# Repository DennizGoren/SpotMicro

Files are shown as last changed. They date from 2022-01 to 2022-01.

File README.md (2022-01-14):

# ROS-based SpotMicro 
TU Delft - Mechanical Engineering (Cognitive Robotics) Bachelor's Thesis

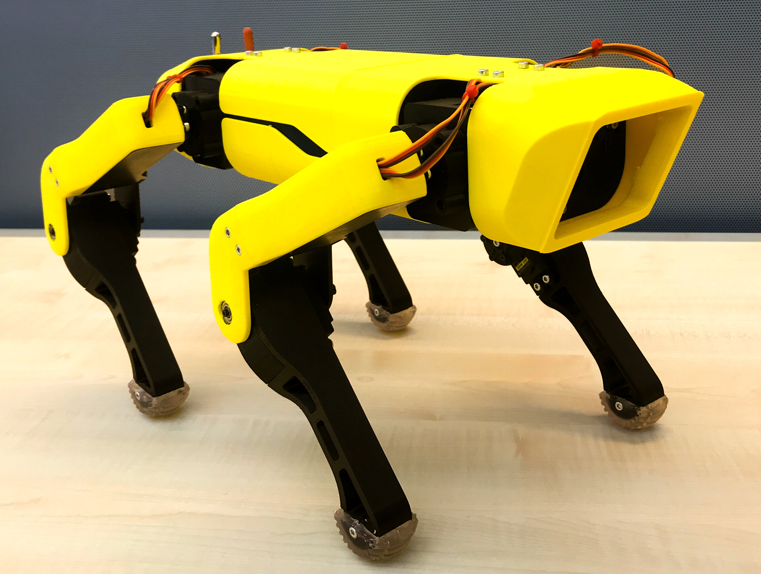
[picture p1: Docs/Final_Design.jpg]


## Introduction
According to 'How robots change the world' by Oxford Economics, Robots could take over 20 million jobs by 2030. It is no longer a question of if robotics will shape our future, but how much and in what ways. This makes teaching young students about robotics all the more important. 

This is the bachelor thesis of four mechanical engineering students of the 3mE faculty at the Delft Technical University. This bachelor thesis was made under the supervision of MSc. Martin Klomp, ir. Ehsan Hosseini and ir. André van der Kraan of the Cognitive Robotics Department.

This report describes the design project called 'Building a low-cost ROS-based Quadruped SpotMicro Robot'. The Cognitive Robotics project has the aim to design a low-cost robot that uses components of the Mirte robot kit. Mirte is a robot developed for education, that includes hardware and software. Mirte was created with the idea that educational robots should be cheap, open source, focus on more than just software, have as few custom parts as possible and should be useful from primary/elementary school all the way to university. 
The Mirte components that are used in the Spotmicro robot are the OrangePi Zero and the STM32 MINI Controller. The software is a python api for ROS, making it possible to control robots from a python script. 

SpotMicro is an opensource robot which takes design elements from the famous spot robot by Boston Dynamics. There are a number of existing designs for the SpotMicro, of which we chose one. Therefore, the design challenge of this project is mostly in research in servo motor selection and the programing of the robot to make SpotMicro work with the Mirte components and software. 

The parts that were used to build the robot were all taken from the SpotMicroESP32 project of Michael Kubina and can be found here:
https://github.com/michaelkubina/SpotMicroESP32

In the simulations folder, the theoretical models for the predictions of the motor torque requirements can be found. All the forward kinametics for the robot control can be found in the code folder. All the STL's that were designed by us for the Mirte hardware can be found in the parts folder.

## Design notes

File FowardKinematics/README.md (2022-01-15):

# Forward Kinematics
The control of the robot was programmed with forward kinematics in Python with the use of the Mirte api for ROS.

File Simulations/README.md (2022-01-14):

In order to predict the minimal required motor torque, multiple
theoretical models were be made. The first model was  a
motion study in Solidworks. Next, a dynamical kinematics
model was be made with the use of Python. From the findings
of the theoretical models, a motor selection was done and
implemented in an actual robot. And lastly, in order to validate
the models, a video analysis of the motion of the robot was
done with the use of Coach 7 and Python.

The SolidWorks motion study modeled the following movements and returned the torques that were deliverd by the motors in the joints. 
The results of this motion study are plotted in the graphs below. 
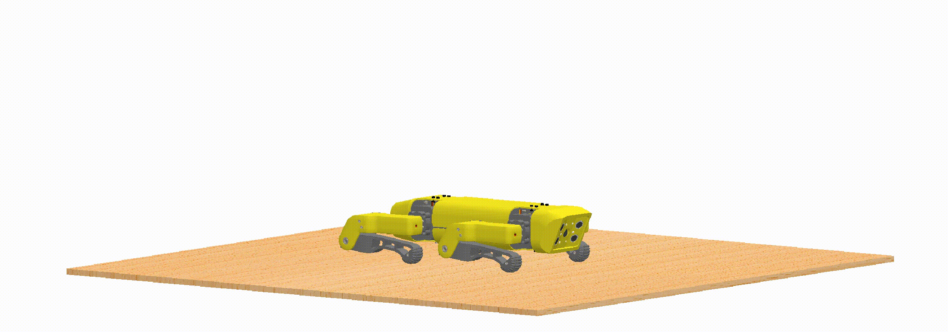
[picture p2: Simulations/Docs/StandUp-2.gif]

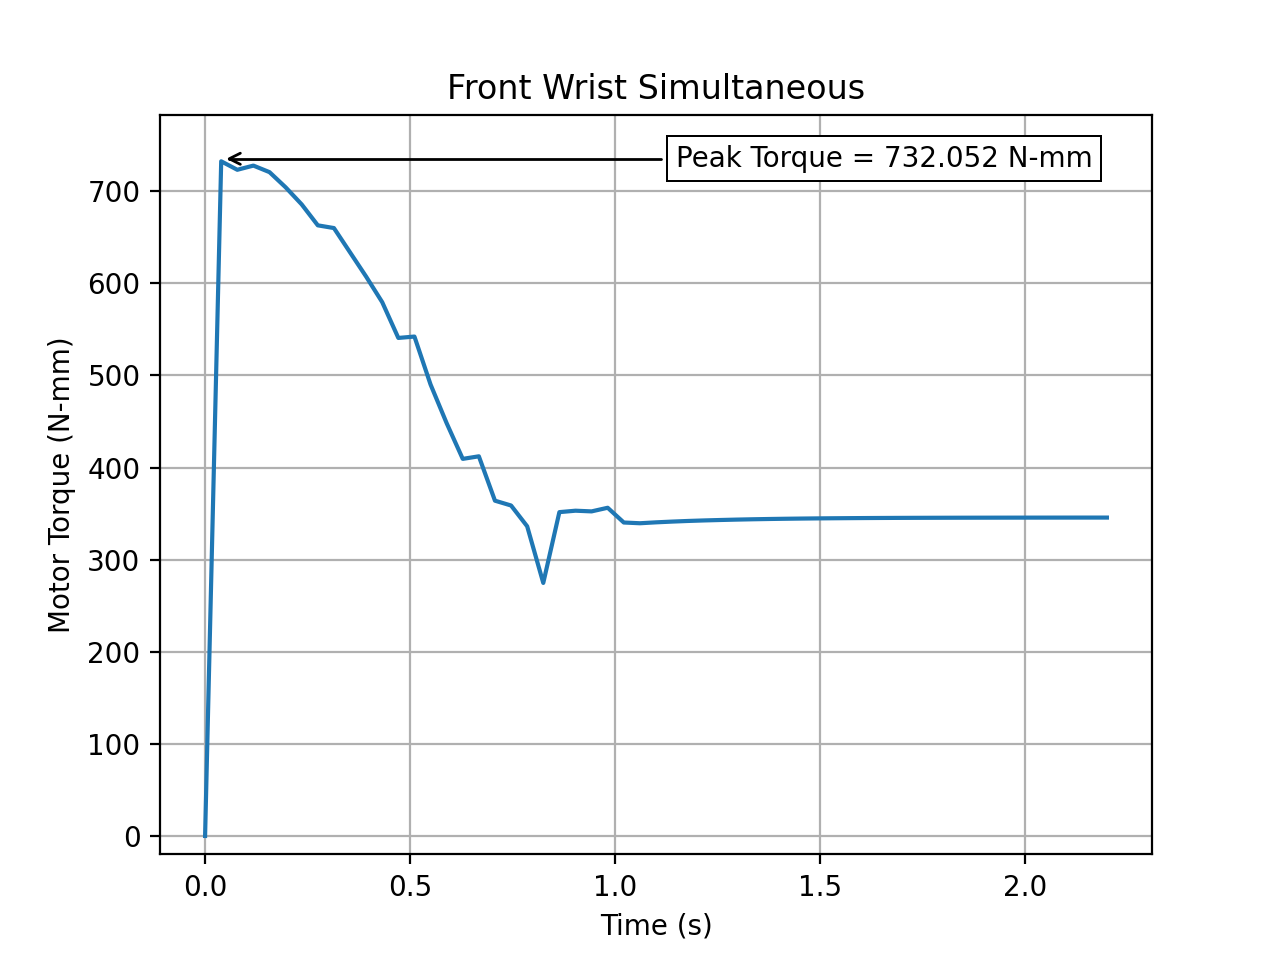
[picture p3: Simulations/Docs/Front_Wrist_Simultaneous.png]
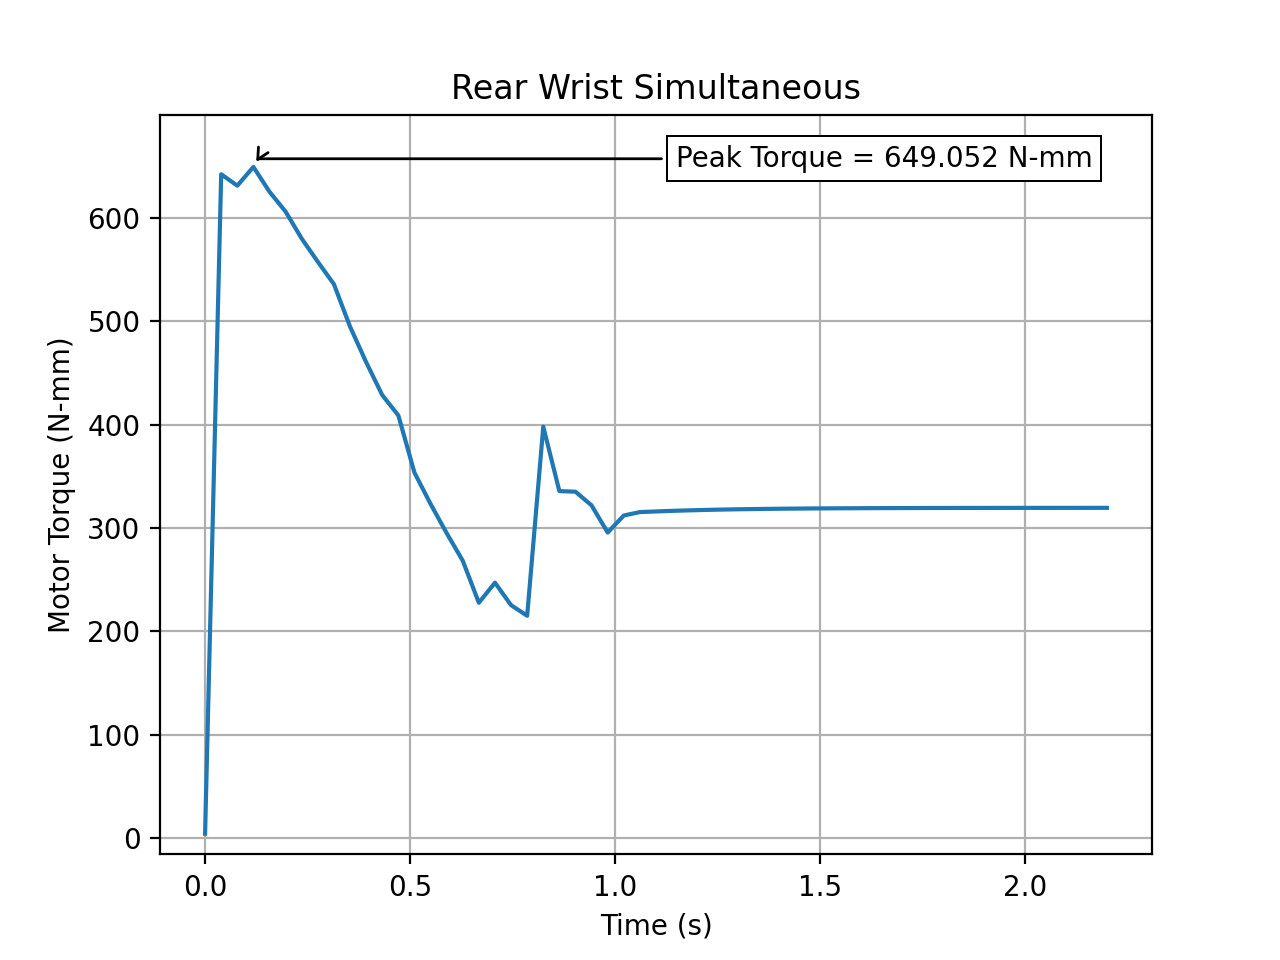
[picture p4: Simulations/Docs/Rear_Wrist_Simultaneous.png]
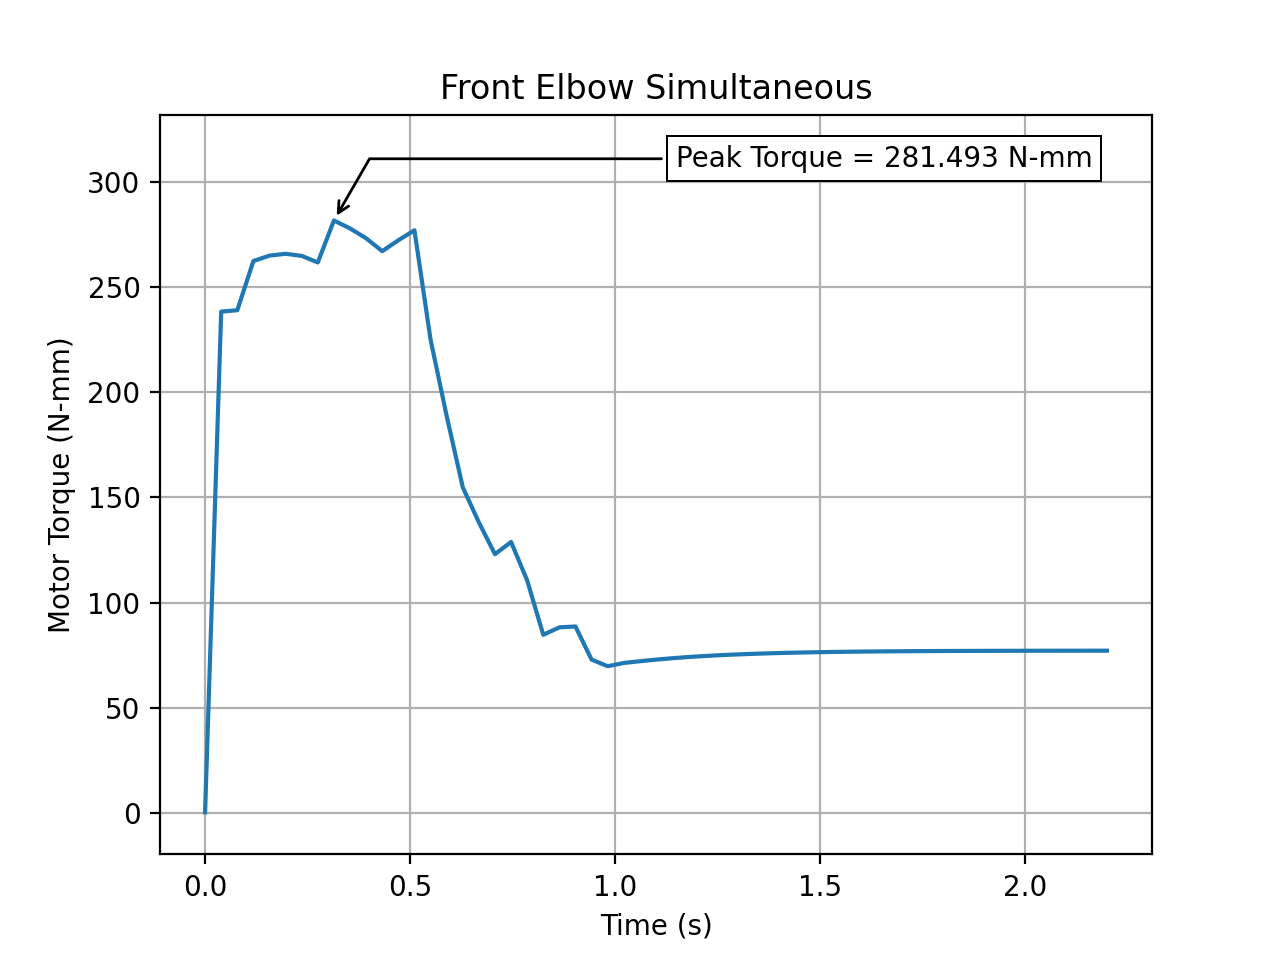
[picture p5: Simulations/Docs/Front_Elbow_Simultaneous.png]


The peak in motor torque is 732 N-mm and witnessed in the wrists of the front legs of the robot.  

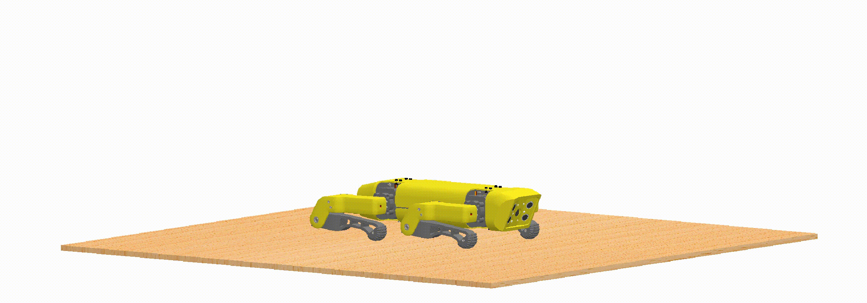
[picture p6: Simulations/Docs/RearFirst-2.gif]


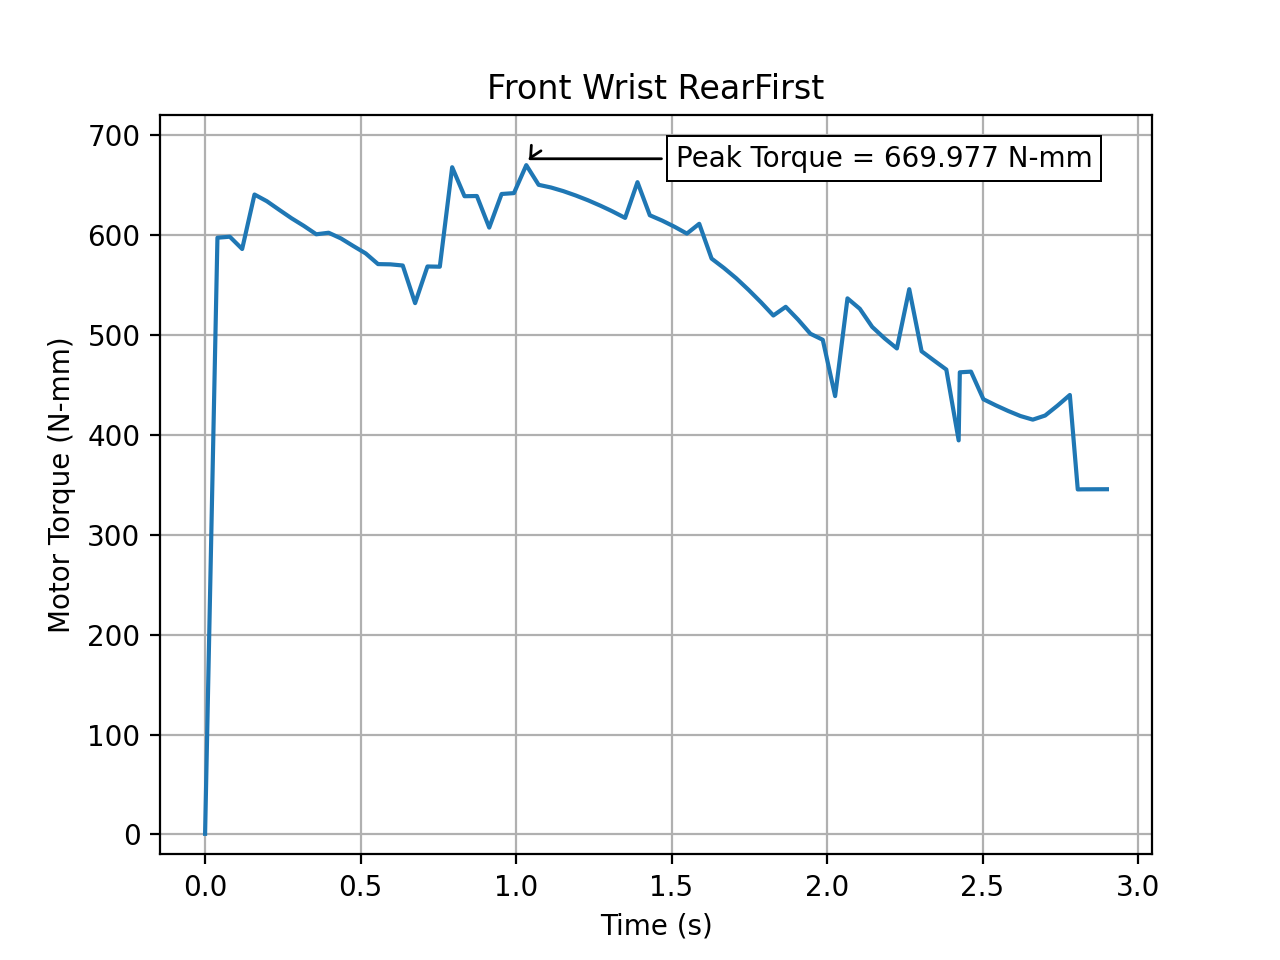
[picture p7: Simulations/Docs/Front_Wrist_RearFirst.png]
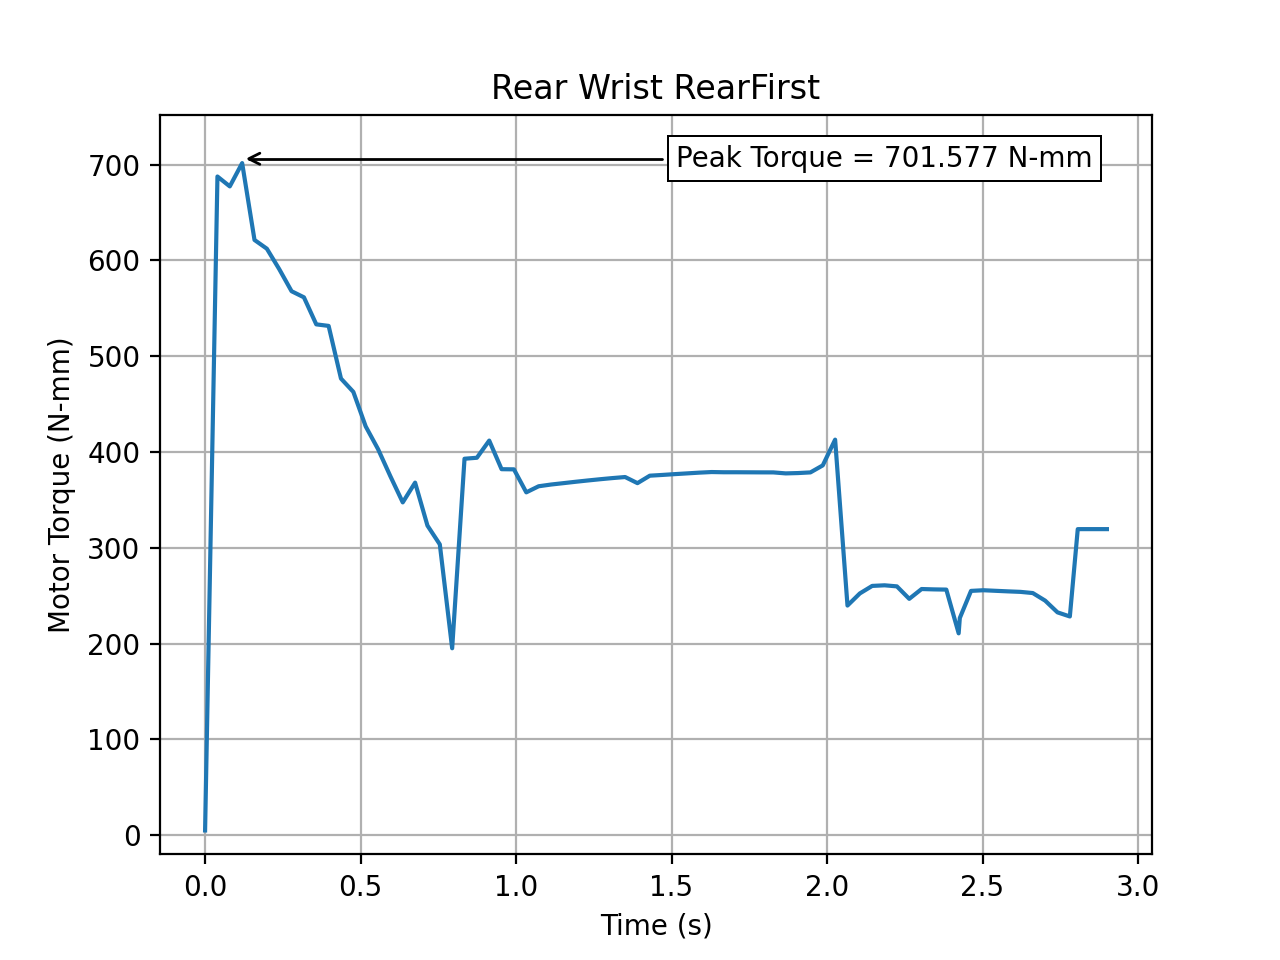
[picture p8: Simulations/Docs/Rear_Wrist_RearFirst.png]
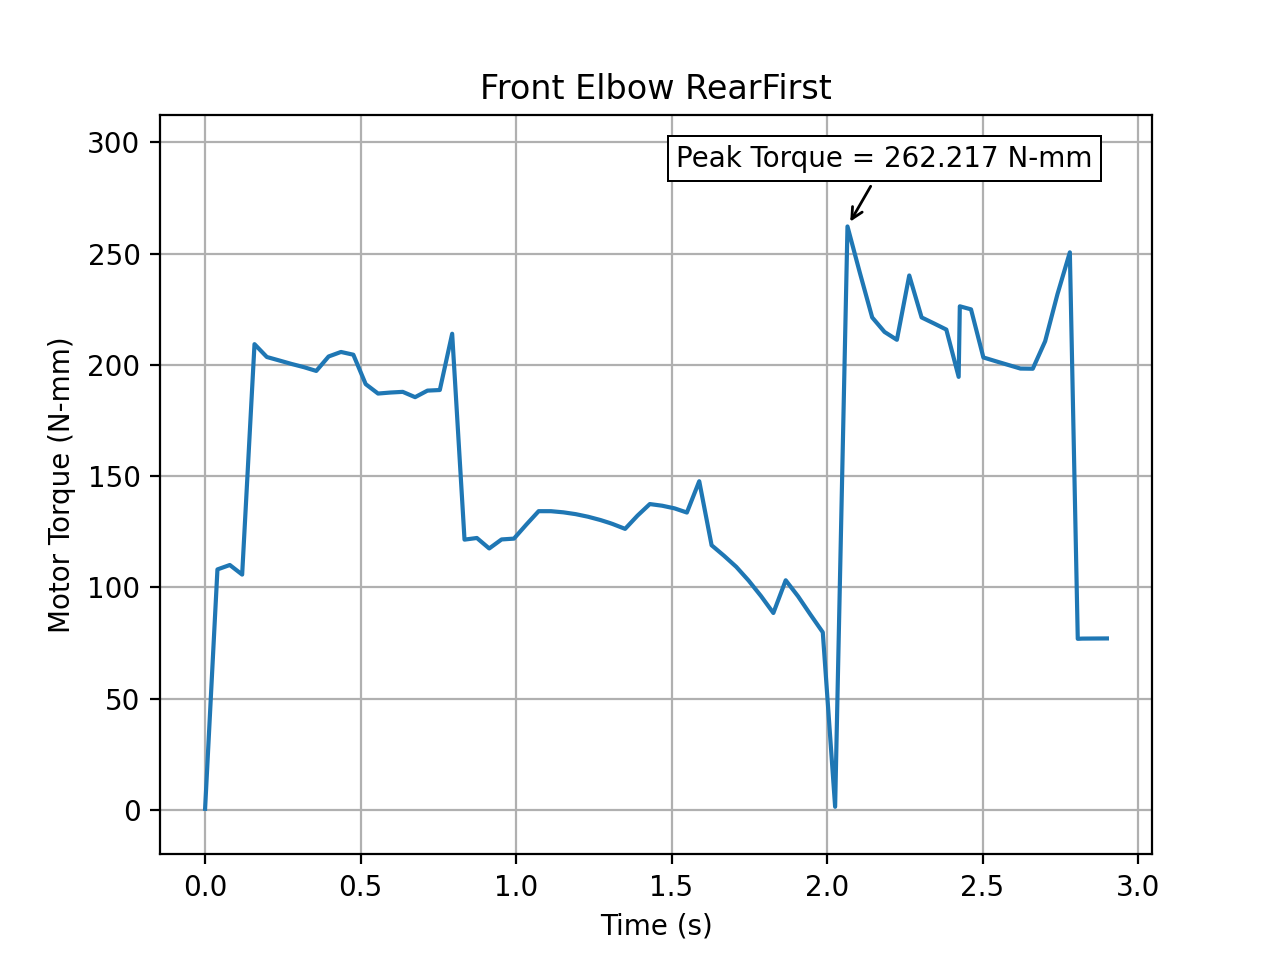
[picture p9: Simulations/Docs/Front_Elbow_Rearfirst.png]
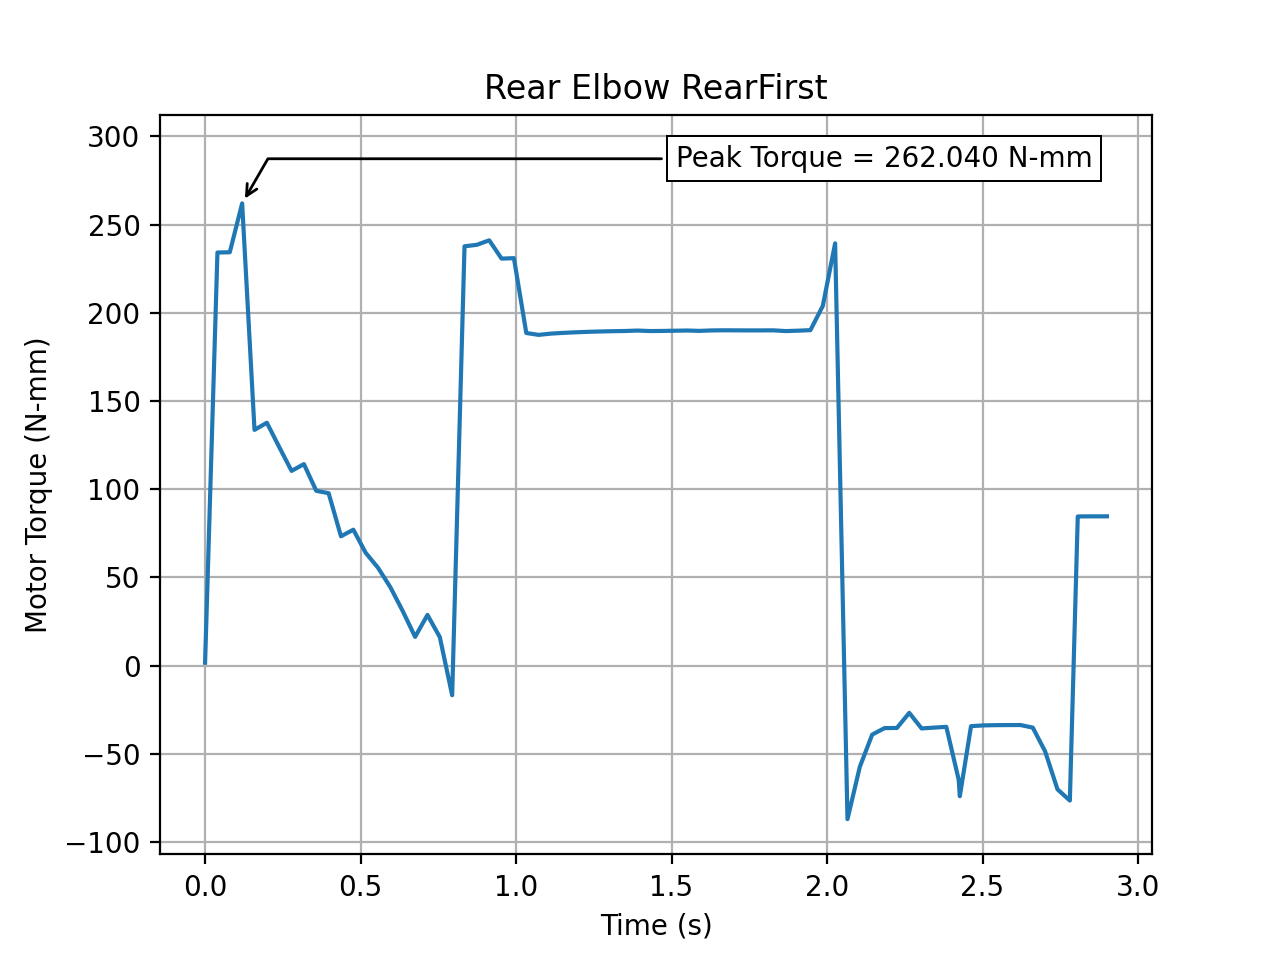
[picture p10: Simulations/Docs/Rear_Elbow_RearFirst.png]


The peak in motor torque is 702 N-mm and witnessed in the wrists of the front legs of the robot.  
From these simulations it became clear that standing up with the rear legs first requires less torque from the motors. 

Next to the motion a study, a dynamical kinematics model was made with the help of a python script. This theoretical model will calculate the required torques based on two components: the force of gravity and the angular momentum of the servo motors. The model simulates the movement of the servomotors: it outputs the velocity and acceleration of the servomotors at their respective position and thus gives an insight in the requirements the motors. See the paper for a more thorough explanation of the model. 
The code of this model can be found in the Code folder. 

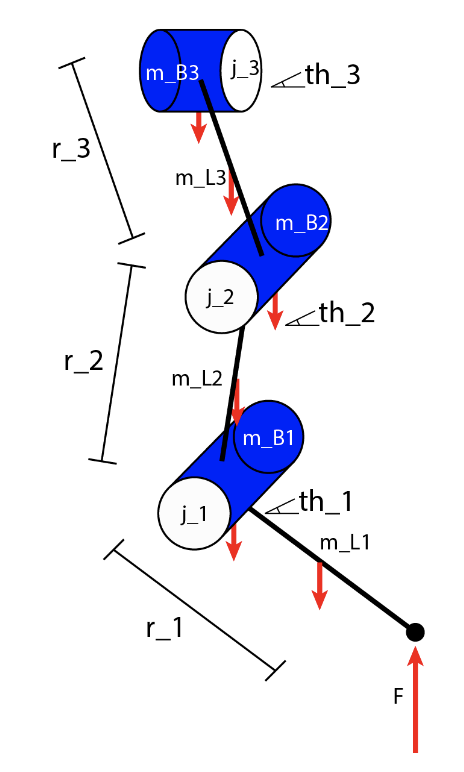
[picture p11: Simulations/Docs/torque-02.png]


After the robot was built, a video analysis of the motion of the robot was made to validate the theoretical models and to find a
conclusive answer to what the real torque is that is required to stand up. The validation is performed on the robot built with
the MG996R servo motors. Coach 7 was used to map out the x and y coordinates of the foot tip, wrist and elbow of the rear and front leg of the robot, a snapshot of this process can be seen below.

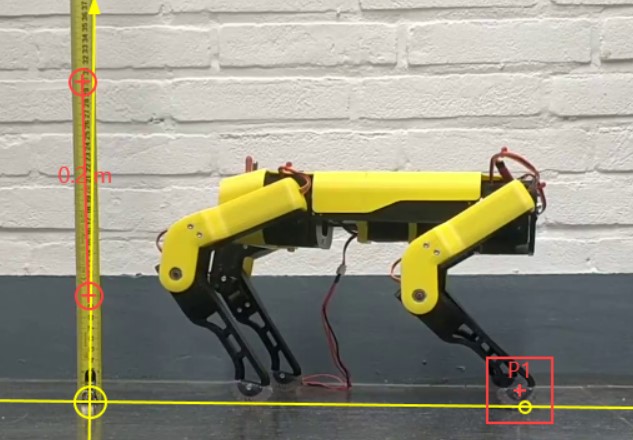
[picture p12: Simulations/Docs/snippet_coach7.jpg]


These coordinates are then imported in a python script that maps out the real angular position, velocity and acceleration of the servomotors. These real coordinates are then used to simulate the movement based on the real movements of the robot, which can be seen in the GIF format here below. It should be noted that because it is still assumed that the robot is symmetric over its longitudinal axis, a profile of the robot is taken.

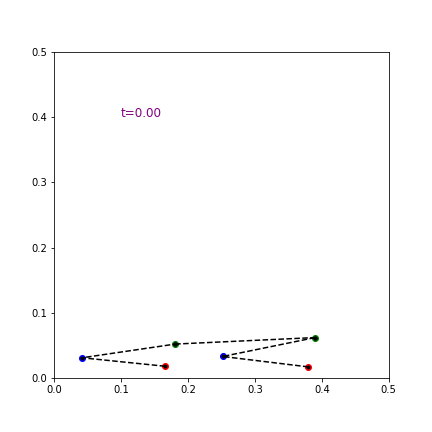
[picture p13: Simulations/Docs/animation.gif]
Coach 7 simulation


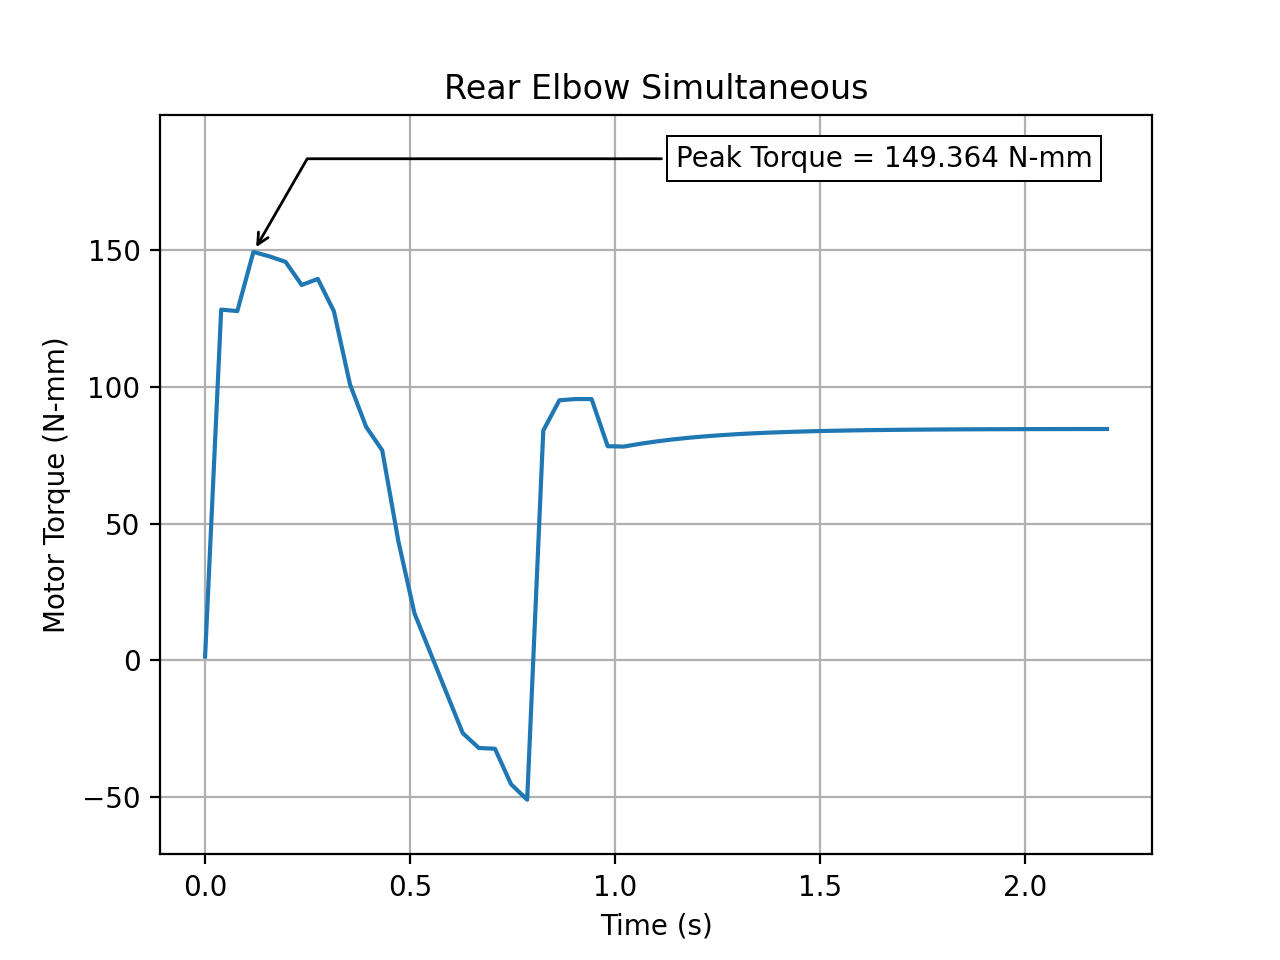
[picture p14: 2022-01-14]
Simulations/Docs/Rear_Elbow_Simultaneous.png

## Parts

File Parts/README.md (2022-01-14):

# Parts and Components

All the STL's that were used to build the robot are from the SpotMicroESP32 project of Michael Kubina and can be found here:
https://github.com/michaelkubina/SpotMicroESP32

The parts that were customized to house the Mirte hardware are all in this folder. They include a mounting plate for the OrangePi Zero, a 5 volt step-down converter and the screw terminals that were used to divide the current to the servo motors. Also a holder for the step-down converter was designed and adjustments were made to the battery holder to house the smaller 6.6 volt lipo battery that was used for this project.  

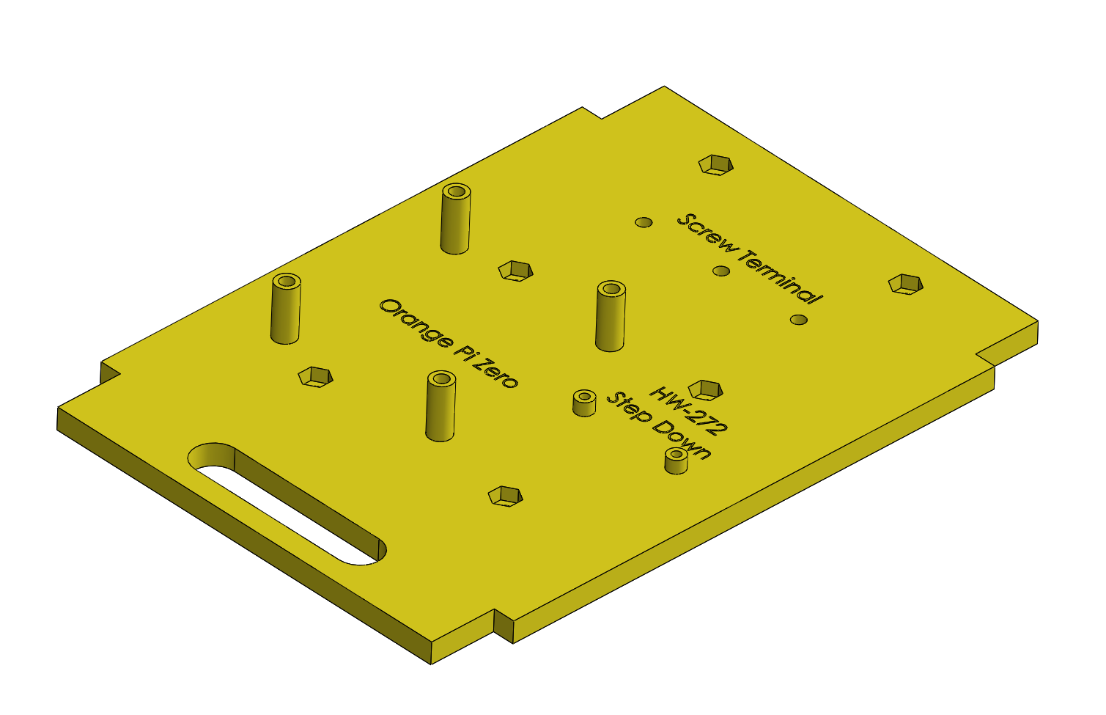
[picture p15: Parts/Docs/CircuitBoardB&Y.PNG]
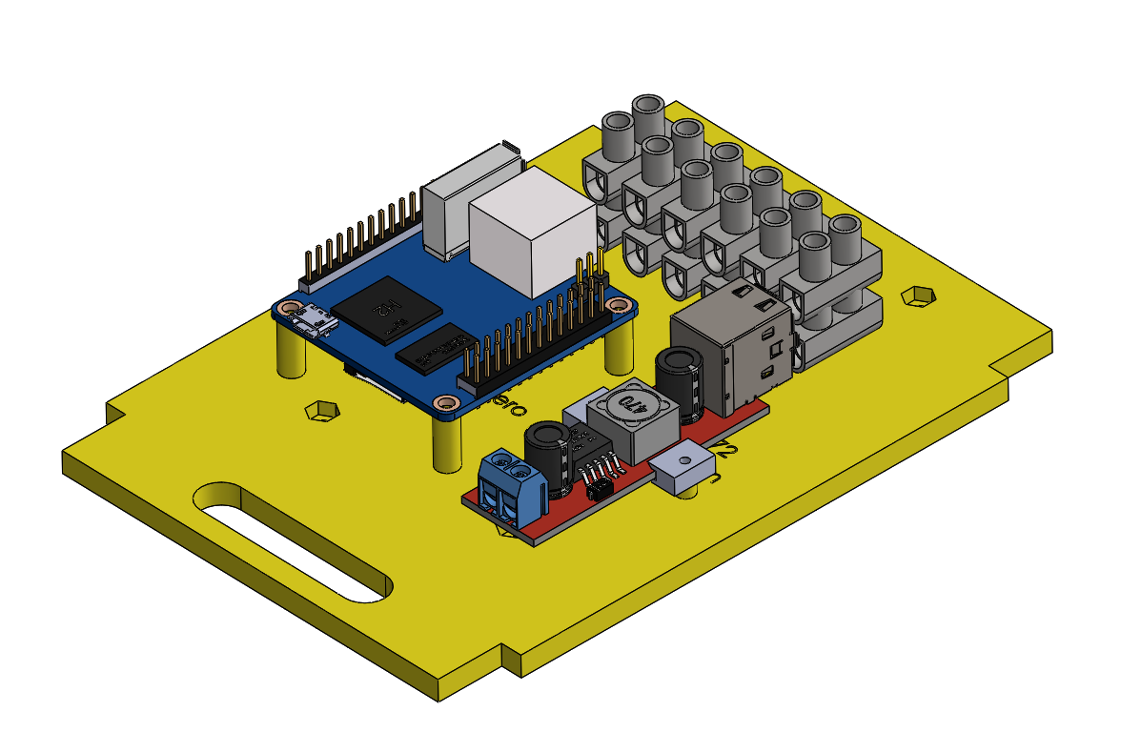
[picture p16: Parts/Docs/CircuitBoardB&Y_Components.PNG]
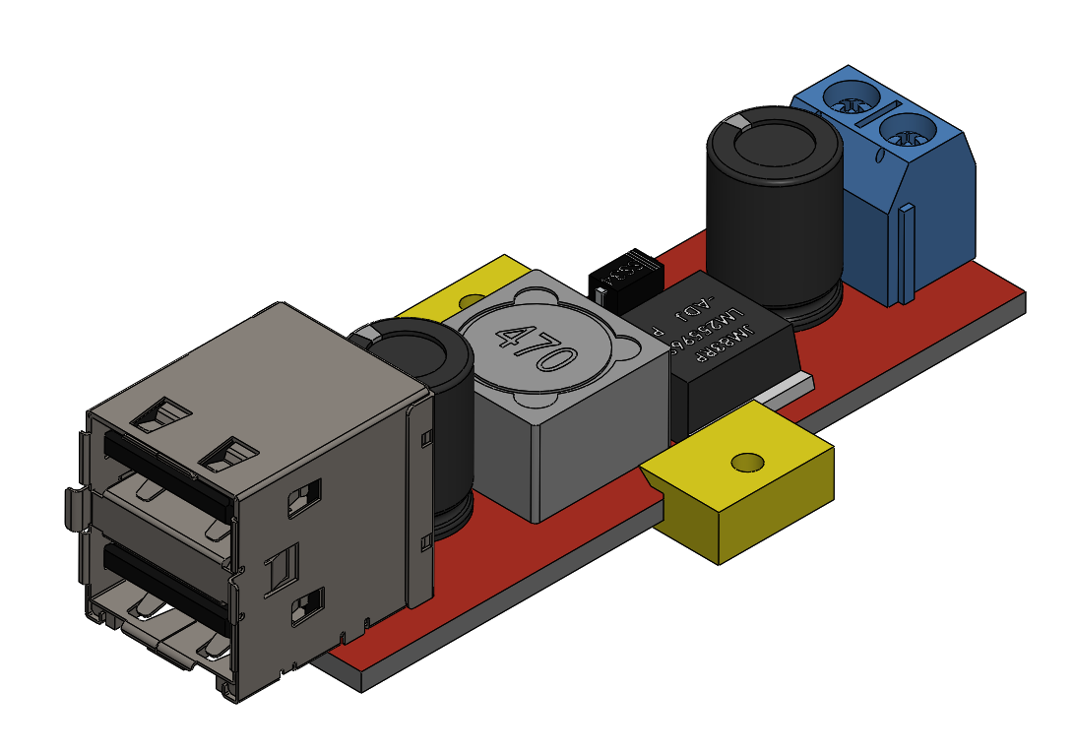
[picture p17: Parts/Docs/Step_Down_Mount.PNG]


Below, a table with all components can be found, along with a price. The components are hyperlinked to sites like Aliexpress, Amazon and Conrad. (Disclaimer: prices are more or less indicative as they tend to vary over time.) 

| **Component** | **Unit Price** | **Quantity** | **Price** | 
| --- | --- | --- | --- |
| [MG996R servomotor](https://nl.aliexpress.com/item/1005002401494033.html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) | €0.95 | 12 | €11.40 |
| [Orange Pi Zero](https://nl.aliexpress.com/item/1005002918902225.html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) | €18.30 | 1 | €18.30 |
| [STM32 Microcontroller](https://nl.aliexpress.com/item/1005002721621360.html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) | €3.28 | 1 | €3.28 |
| [Micro SD Card (at least 16 GB)](https://nl.aliexpress.com/item/1005003698975403.html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)| €1.52 | 1 | €€1.52 |
| [PLA for 3D print design](https://www.amazon.nl/filament-printers-stiften-diameter-kleur/dp/B08D79V39W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) | €18.00(€/kg) | 1 kg | €18.00 |
| [Terminal blocks](https://www.amazon.nl/Fixpoint-77008-kroonluchter-mm²-transparant/dp/B000V8GR9O/ref=asc_df_B000V8GR9O/?tag=nlshogostdde-21&linkCode=df0&hvadid=430516654065&hvpos=&hvnetw=g&hvrand=7825961289045030379&hvpone=&hvptwo=&hvqmt=&hvdev=c&hvdvcmdl=&hvlocint=&hvlocphy=9102681&hvtargid=pla-563290875765&psc=1) | €0.75 | 2 | €1.50 |
| [USB step down converter](https://nl.aliexpress.com/item/4001333967589.html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) | €0.79 | 1 | €0.79 |
| [LiPo battery pack](https://www.conrad.nl/p/hacker-life-accupack-66-v-2100-mah-aantal-cellen-2-30-c-softcase-xt60-2178343) | €28.50 | 1 | €28.50 |
| [XT60 cable](https://www.conrad.nl/p/modelcraft-58378-10-accu-kabel-1x-xt60-stekker-1x-open-kabeleinde-1000-cm-40-mm-1235115) | €6.60 | 1 | €6.60 |
| [Pack of jumper cables](https://www.otronic.nl/a-60558956/draden-en-kabels/dupont-jumper-kabels-40-stuks-male-female-10cm-draadbruggen-voor-breadboard/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) | €1.79 | 1 | €1.79 |
| [4mm2 Electrical cable](https://www.elektramat.nl/aansluitdraad-4-mm-zwart-per-meter/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) | €0.86 (€/m) | 0.30m | €0.26 |
| [Toggle switch](https://www.amazon.nl/PEREL-8013AC-tuimelschakelaar-verticaal-aan-één/dp/B01E03NGLC/ref=sr_1_64?__mk_nl_NL=ÅMÅŽÕÑ&keywords=tuimelschakelaar&qid=1642166485&sr=8-64) | €2.13 | 2 | €4.26 |
| [M3 nuts](https://www.toolstation.nl/zeskantmoer/p20200) | €1.35 | 1 | €1.35 |
| [M2 nuts](https://www.toolstation.nl/zeskantmoer/p20199) | €1.35 | 1 | €1.35 |
| [M3x8 bolts](https://www.123-3d.nl/123-3D-Metaalschroef-inbus-M3x8-cilinderkop-verzinkt-50-stuks-i3078-t3122.html) | €2.05 | 2 | €4.10 |
| [M3x20 bolts](https://www.123-3d.nl/123-3D-Metaalschroef-inbus-M3x20-cilinderkop-verzinkt-50-stuks-i1175-t3122.html) | €2.95 | 2 | €5.90 |
| [M2x8 bolts](https://www.123-3d.nl/123-3D-Metaalschroef-bolkop-M2x8-verzinkt-50-stuks-i4739-t16149.html) | €2.75 | 2 | €5.50 |
| [Ball bearing](https://www.conrad.nl/p/reely-kogellager-radiaal-chroomstaal-binnendiameter-5-mm-buitendiameter-16-mm-toerental-max-43000-omwmin-214442) | €2.65 | 8 | €20.48 |
| **Total** | | | **€134.88** |

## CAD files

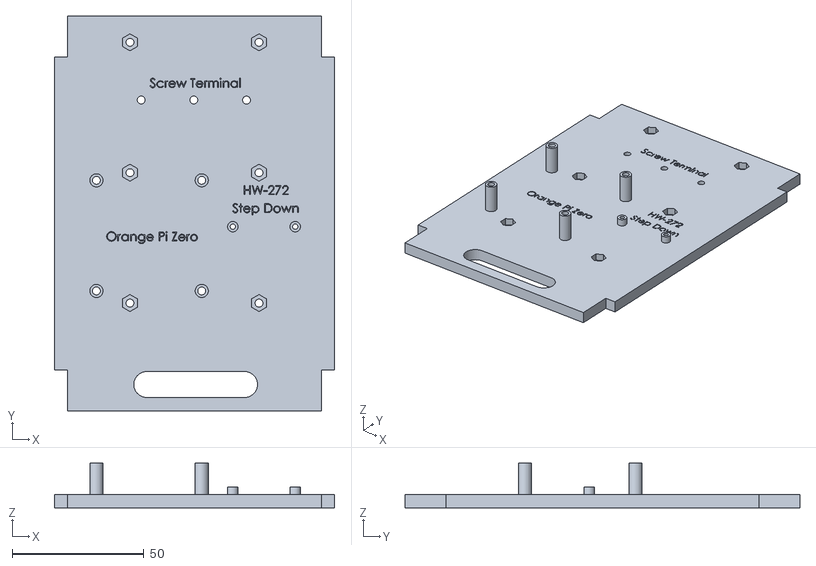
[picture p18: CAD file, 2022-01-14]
Parts/STL's/Circuit_Board_Mounting_Plate.STL
106.5 x 150.0 x 17.0

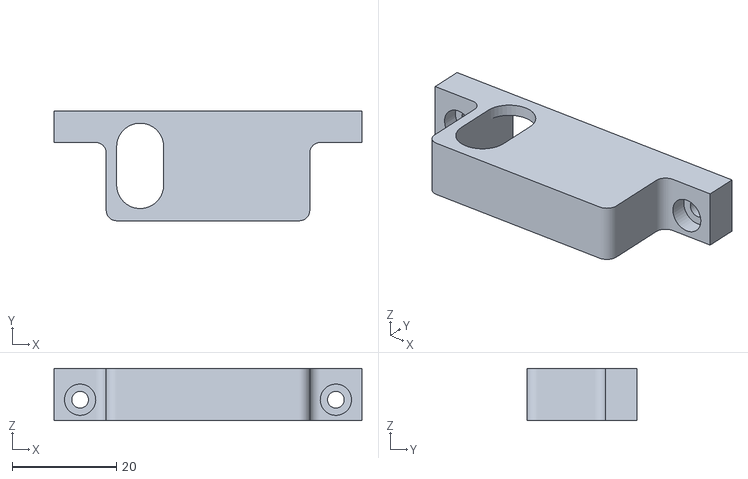
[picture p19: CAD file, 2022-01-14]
Parts/STL's/Lipo_Mount_End_Cap_With_Cable_Hole.STL
59.0 x 21.0 x 10.0

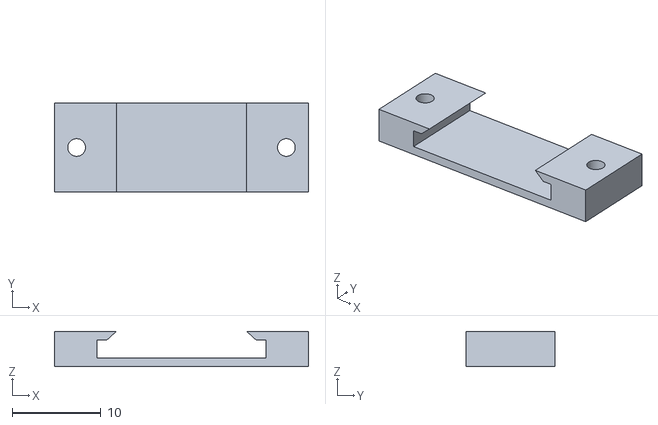
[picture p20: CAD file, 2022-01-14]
Parts/STL's/Step_Down_Mount.STL
28.7 x 10.0 x 4.00

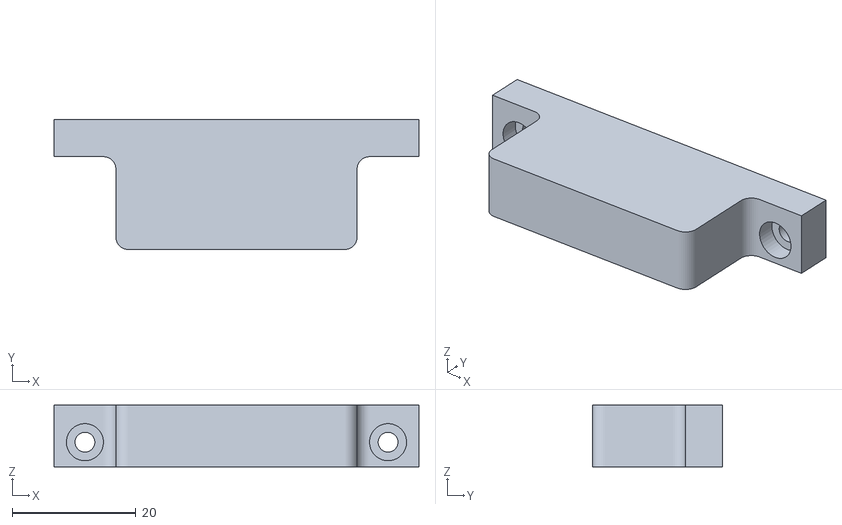
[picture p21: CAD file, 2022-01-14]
Parts/STL's/Lipo_Mount_End_Cap.STL
59.0 x 21.0 x 10.0

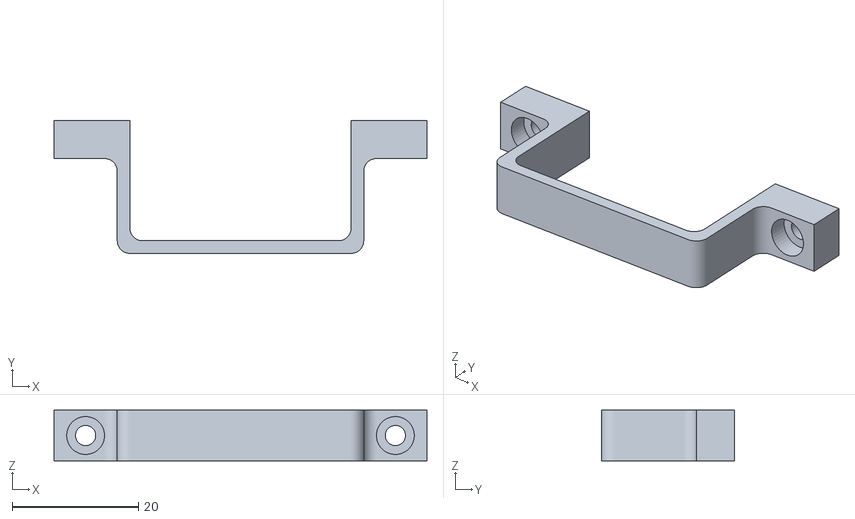
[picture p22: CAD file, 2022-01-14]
Parts/STL's/Lipo_Mount_Middle.STL
59.0 x 21.0 x 8.00

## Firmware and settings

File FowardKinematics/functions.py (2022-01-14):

import time
from mirte_robot import robot
mirte = robot.createRobot()

# Starting in a laying position
def start():
	mirte.setServoAngle('1', 12)
	mirte.setServoAngle('2', 155)
	mirte.setServoAngle('3', 97)
	mirte.setServoAngle('4', 100)
	mirte.setServoAngle('5', 17)
	mirte.setServoAngle('6', 81)
	mirte.setServoAngle('7', 15)
	mirte.setServoAngle('8', 160)
	mirte.setServoAngle('9', 83)
	mirte.setServoAngle('10', 162)
	mirte.setServoAngle('11', 15)
	mirte.setServoAngle('12', 97)

# Going to the laying position in a controlled manner 
def lay():
	mirte.setServoAngle('1', 50)
	mirte.setServoAngle('2', 140)
	mirte.setServoAngle('3', 97)
	mirte.setServoAngle('4', 62)
	mirte.setServoAngle('5', 36)
	mirte.setServoAngle('6', 81)
	mirte.setServoAngle('7', 55)
	mirte.setServoAngle('8', 143)
	mirte.setServoAngle('9', 83)
	mirte.setServoAngle('10', 121)
	mirte.setServoAngle('11', 31)
	mirte.setServoAngle('12', 97)
	time.sleep(1)
	mirte.setServoAngle('1', 12)
	mirte.setServoAngle('2', 155)
	mirte.setServoAngle('3', 97)
	mirte.setServoAngle('4', 100)
	mirte.setServoAngle('5', 17)
	mirte.setServoAngle('6', 81)
	mirte.setServoAngle('7', 15)
	mirte.setServoAngle('8', 160)
	mirte.setServoAngle('9', 83)
	mirte.setServoAngle('10', 162)
	mirte.setServoAngle('11', 15)
	mirte.setServoAngle('12', 97)


# Standing up with the rear legs first
def stretch():
	mirte.setServoAngle('7', 95)
	mirte.setServoAngle('8', 125)
	mirte.setServoAngle('9', 83)
	mirte.setServoAngle('10', 80)
	mirte.setServoAngle('11', 47)
	mirte.setServoAngle('12', 97)
	time.sleep(0.5)
	mirte.setServoAngle('1', 88)
	mirte.setServoAngle('2', 125)
	mirte.setServoAngle('3', 100)
	mirte.setServoAngle('4', 20)
	mirte.setServoAngle('5', 55)
	mirte.setServoAngle('6', 80)

# Giving a paw for 3 seconds
def paw():
    mirte.setServoAngle('1', 88)
    mirte.setServoAngle('2', 125)
    mirte.setServoAngle('3', 100)
    mirte.setServoAngle('4', 20)
    mirte.setServoAngle('5', 55)
    mirte.setServoAngle('6', 80)
    mirte.setServoAngle('7', 95)
    mirte.setServoAngle('8', 125)
    mirte.setServoAngle('9', 83)
    mirte.setServoAngle('10', 80 + 30)
    mirte.setServoAngle('11', 47 - 20)
    mirte.setServoAngle('12', 97)
    time.sleep(0.5)
    mirte.setServoAngle('2', 125-80)
    time.sleep(3)
    mirte.setServoAngle('2', 125)
    time.sleep(0.5)
    mirte.setServoAngle('10', 80)
    mirte.setServoAngle('11', 47)
    
# Making one step in the forward direction
def forward():
	a = 10
	b = 5
	c = 2
	d = 10
	sleep = 0.2

	mirte.setServoAngle('4', 20 - a)
	mirte.setServoAngle('5', 55 - b)
	mirte.setServoAngle('7', 95 + a)
	mirte.setServoAngle('8', 125 + b)
	time.sleep(sleep)
	mirte.setServoAngle('4', 20 + c)
	mirte.setServoAngle('5', 55 - d)
	mirte.setServoAngle('7', 95 - c)
	mirte.setServoAngle('8', 125 + d)
	time.sleep(sleep)
	mirte.setServoAngle('4', 20 + b)
	mirte.setServoAngle('5', 55)
	mirte.setServoAngle('7', 95 - b)
	mirte.setServoAngle('8', 125)
	time.sleep(sleep)
	mirte.setServoAngle('4', 20)
	mirte.setServoAngle('7', 95)
	mirte.setServoAngle('1', 88 + a)
	mirte.setServoAngle('2', 125 + b)
	mirte.setServoAngle('10', 80 - a)
	mirte.setServoAngle('11', 47 - b)
	time.sleep(sleep)
	mirte.setServoAngle('1', 88 - c)
	mirte.setServoAngle('2', 125 + d)
	mirte.setServoAngle('10', 80 + c)
	mirte.setServoAngle('11', 47 - d)
	time.sleep(sleep)
	mirte.setServoAngle('1', 88 - b)
	mirte.setServoAngle('2', 125)
	mirte.setServoAngle('10', 80 + b)
	mirte.setServoAngle('11', 47)
	time.sleep(sleep)
	mirte.setServoAngle('1', 88)
	mirte.setServoAngle('10', 80)

	# Making one step in the backward direction
def backward():
	a = 10
	b = 5
	c = 2
	d = 10
	sleep = 0.2

	mirte.setServoAngle('4', 20 - a)
	mirte.setServoAngle('5', 55 + b)
	mirte.setServoAngle('7', 95 + a)
	mirte.setServoAngle('8', 125 - b)
	time.sleep(sleep)
	mirte.setServoAngle('4', 20 - a)
	mirte.setServoAngle('5', 55 + d)
	mirte.setServoAngle('7', 95 + a)
	mirte.setServoAngle('8', 125 - d)
	time.sleep(sleep)
	mirte.setServoAngle('4', 20 + b)
	mirte.setServoAngle('5', 55)
	mirte.setServoAngle('7', 95 - b)
	mirte.setServoAngle('8', 125)
	time.sleep(sleep)
	mirte.setServoAngle('4', 20)
	mirte.setServoAngle('7', 95)
	mirte.setServoAngle('1', 88 + a)
	mirte.setServoAngle('2', 125 - b)
	mirte.setServoAngle('10', 80 - a)
	mirte.setServoAngle('11', 47 + b)
	time.sleep(sleep)
	mirte.setServoAngle('1', 88 + a)
	mirte.setServoAngle('2', 125 - d)
	mirte.setServoAngle('10', 80 - a)
	mirte.setServoAngle('11', 47 + d)
	time.sleep(sleep)
	mirte.setServoAngle('1', 88 - b)
	mirte.setServoAngle('2', 125)
	mirte.setServoAngle('10', 80 + b)
	mirte.setServoAngle('11', 47)
	time.sleep(sleep)
	mirte.setServoAngle('1', 88)
	mirte.setServoAngle('10', 80)


# Making one step in the forward direction
def slow():
	a = 15
	b = 10
	c = 5
	d = 10
	e = 20
	sleep = 0.2

	mirte.setServoAngle('7', 95 - a)
	time.sleep(0.5)
	mirte.setServoAngle('4', 20 + b)
	mirte.setServoAngle('5', 55 - c)
	time.sleep(0.5)
	mirte.setServoAngle('5', 55 + d)
	time.sleep(0.5)
	mirte.setServoAngle('7', 95)
	mirte.setServoAngle('4', 20 + e)
	time.sleep(0.5)
	mirte.setServoAngle('7', 95 - b)
	mirte.setServoAngle('8', 125 + c)
	time.sleep(0.5)
	mirte.setServoAngle('8', 125 - d)
